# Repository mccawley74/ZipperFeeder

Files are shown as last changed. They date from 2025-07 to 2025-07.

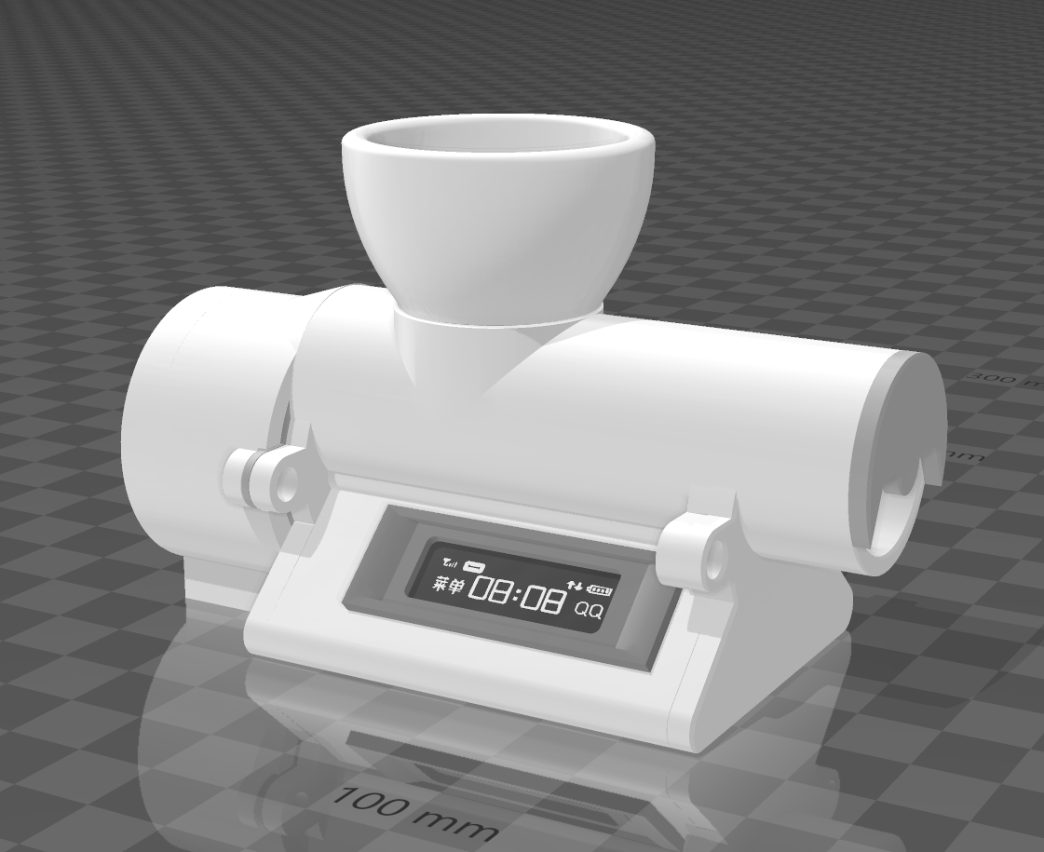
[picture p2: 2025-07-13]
Images/assembled.png

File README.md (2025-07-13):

Non-Commercial license You are free to: Share --- copy and redistribute
the material in any medium or format freely. Adapt --- remix, transform,
and build upon the material for any purpose, except commercially.

Attribution Heavily modified from: \"MiniFeeder\" By GK-3D
https://www.thingiverse.com/thing:4361894

# BACKGROUND
I made this feeder as I have a Pico Reef Tank (Two Gallon) with one
fish, my Gobi. Looking around for a small feeder was not successful,
most all were the size of my tanks lid blocked the light and held too
much food.

Since I had all these parts, I made the smallest feeder I could.

And if you are wondering why it is called Zipper Feeder, it is because I
have a Striped Goby that I named Zipper. You will see this name in the
OLED menu as well. I did make it so the name is a variable in code:
String fish_name = \"ZIPPER\"; Line 92 I believe, in
\"zipper_feeder.ino\"

## Pros
 1. Small, very small 2. Simi programmable feed schedule with OLED
screen 3. Nano feed rate. Good for 1-3 small fish 4. DIY abd fun to
build, unless you have sausage fingers :( 5. Customizable if you do any
3D modeling and/or Arduino development.

## Cons
1. Does NOT have an RTC clock. I.e. no time keeping, uses time since boot to track schedule.
2. Only programmable to feed every six hours, or every three hours. With option to skip nights.
3. The amount of food it dispenses is based on the Auger size. I included two:
    - auger_larger.stl Has larger spacing, allowing more food per rotation.
    - auger_smaller.stl Has smaller spacing, allowing less food per rotation.

You can print each individually or both with file \"auger_both.stl\" and
test each.

4. Hard to assemble due to small size. 5. Manual alignment of the Auger. Only needs done once. Could be added to code (Have a go!) 6. Some manual modifications needed. I.e OLED mounting, button location and hole, screw
choice.

7. No screw standard. I used what I had, what fit. The front cover is pass-through (Nut bolt) The rear cover and motor cover/motor mounting is
self threading screws.

8. NOT battery powered, needs USB 5v

NO: It does not overheat in such a small space. It really doesn\'t do anything until it feeds. The motor is external of the main chassis, runs only every 3 hours minimum, etc\... There is however a vented front cover \"front_cover_vented.stl\" if you are paranoid.

## BOM Item Description Cost

| Item |Description | Cost |
| --- | --- |  --- |
Control Board:  |  Arduino Pro Micro 5v                          |  $6.50 Ea.
Motor:          |  28BYJ-48 Stepper Motor                        |  $2.50
Motor CTRL:     |  ULN2003 Driver Board                          |  $2.50
Button:         |  Micro Momentary Tactile Push Button           |  $0.05
Wire:           |  30AWG 8-Color Tinned Copper Solid Cable       |  $0.10
Display:        |  0.91" I2C OLED Display SSD1306 128x32 3.3V/5V |  $4.00
Housing:        |  Overture PLA                                  |  $1.00

Per part prices are based off of Amazon and include the breakdown cost
used, I.e: - OLED screen comes as a two for \$8.00 - A spool of wire is
\$9.00 - The motor and motor control board come as a pair for \$5.00

If you search Amazon/AliExpress with the search term being the above
Description you should easily find the part(s)

Yes, you can buy a decent feeder for around \$20.00, but if you already
have some parts and you want a super tiny feeder, and love to make
stuff. Keep reading.

If you want the best automatic feeder I\'ve found to date, look at the
Petbank Store \"Automatic Fish Feeder\" It\'s is a round carousel style
USB re-chargeable feeder with LCD that lasts for weeks. Not affiliated,
just have two now for my larger tanks and they work great.

### ASSEMBLY: Sorta, Don\'t hate me after this part.
---
You will need thin wire to allow for the reduced space. I use 30AWG wire
in most all my Arduino projects. Specifically \"8-Color Electronic
Wire - 30 AWG Single Core, 250M Tinned Copper Solid Cable for Circuit
Boards & PCB\" You can find it on Amazon. Just search for the above
mentioned.

There is no schematic for this project. All connections are detailed in
the header comments of the Arduino code:
/Code/zipper_feeder/zipper_feeder.ino

The assembly takes the most time and patience. I did some tweaking of
the files after I assembled mine to make things a bit easier.

Things to note. There are two motor controller boards you will find on
Amazon/AliExpress, etc the first is a square type the other is a smaller
rectangle shape.


While the square type had better motor control when it came to the
smoothness of the movement at low speeds, the rectangle shaped board was
a lot easier to fit in the chassis. The Chassis was designed for the
square board so either will work. Your choice.

Both of these boards can be found with a motor on Amazon/AliExpress with
a motor. The motor will be: 28BYJ-48 Geared Stepper Motor DC 5V The
board will be one of: ULN2003 Driver Board, or L293D Motor Drive Module
DC4.5-25V

For either of the two motor control boards you choose, you will need to
cut down the connection header pins, or de-solder altogether. (I
de-soldered for best clearance)

### Assembly Steps:
1. Lay the printed chassis on your workplace.
2. Place the motor, Arduino, and OLED display on the left of the chassis.
3. Place the motor module to the right of the chassis.
4. Lay out your wire from the Arduino to the Motor Control board so as
there is enough to pass through the chassis and reach the control board.

5. Cut the motor wires down so that there is just enough length to also
reach the control board but still leave the motor with a good inch
clearance from the chassis. See image: motor-mounting.png You will want
enough slack, once the motor board in installed to pull the motor off
the auger. See Image: assembly-2.png for a cutaway chassis diagram.

6. Set the chassis aside and lay out the parts in the order shown in
image: wire-two.png Solder the motor wires to the control board, the
control board to the Arduino. The OLED to the Arduino (Leave wire slack)
etc\... The images should help.

7. Glue the main chassis to the Auger tube (CA Glue) Place the main
chassis on a flat surface and apply glue to the top of the chassis,
while holding the auger tube, place onto the top of the chassis and hold
in place until dry. The auger tube rear flange should butt up against
the rear main chassis. See: \"tube_alignment.png\"

You can temporarily mount the motor cover to the auger tube as the
bottom of the motor cover will lay flat against the work surface along
with the main chassis, this will allow the tube and chassis to remain
properly aligned with one another while the glue dries.

8. Mount the OLED, after the OLED in in place use CA Glue to align and
affix the screen bezel.

9. Align and mount your button. Use glue to hold in place. NOTE: You
will notice that the chassis STL does not have a button hole. The first
model I Made did not have any menu or programmability and thus no
button. I added it later and as such I simply drilled a hole and glued a
small Tactile switch I had in place. Feel free to use any button you may
have, put where you want (Fits) Or even use two buttons and update the
code. There are plenty of free GPIO ports to work with. I am sure the
code can be improved upon.

10. Insert the Arduino into the chassis. slide in and then to the rear,
making sure the USB port properly slides into the USB hole in the
chassis. Use a bit of PLA, toothpick, etc. to wedge the Arduino in
place. see image: board-mounting.png

11. Slide the motor control board into the chassis and install the
front cover.

12. Install the rear cover, making sure that the motor wires pass
through the slot in the cover.

13. Slide the Auger into the chassis tube and press into the motor,
aligning the slot in the auger to that of the motor. If too tight heat
the motor shaft so it more readily slides into the PLA Or ensure that
the Auger and motor shaft fit ahead of time.

14. Slide the motor_cover.stl over the motor and install screws to
secure the motor cover, and motor to the chassis. Again see images in
the images folder for help.

15. Use CA Glue to affix the hopper and Auger tube cap.

16. Connect to your computer and flash with the included code.

**NOTE:** The auger tube cap keeps the auger from accidentally coming off
the motor shaft and sliding out the end of the tube. While it does make
removing the Auger a bit more difficult as it can only exit the rear of
the housing after removing the motor cover, and motor, it does keep the
Auger in place.

If you use the smaller rectangle shaped motor control board it
will slide in from the same side of chassis as the Arduino (Left) At a
slight tilted angle.

As of now, there is no recess, or specific mount for the OLED. It will
just fit into the opening. from the inside of the chassis. Once you have
it in place, use CA Glue, hot glue, or a PLA pen to hold in place
permanently. (Or edit the STL files)

Be patient. I wasn\'t sure at first if all the parts would fit, and
fought for a while before coming up with the method shown in the images.
I did manage to fit the larger square control board before re-designing
the chassis and using a smaller board as de-soldering that many pins was
tedious and I figured anyone making one of these would hate me just a
little less.

If you leave the Arduino an inch outside the chassis (left), and the
motor control board 1 inch outside the chassis (right), and measure out
the wire length, and use half that length for the OLED, it will all
stuff in the chassis nicely.

It\'s all easy to put in but becomes a bit fiddly once the OLED is glued
in place as the Arduino board, and motor have only an inch or so of
play.

### MENU SYSTEM
---
1. Press the button once to enter the menu system.
2. Each press of the button will move to the next menu setting.
3. Hold the button down for one second to select that menu item

**NOTE:** If you reach the end of the menu it will round robin back to the
start.

Each menu setting is listed below as it appears on the screen.

#### Id Grouping Item
---
1. Menu \| Options Load Food
2. Menu \| Feed Feed Now
3. Menu \| Feed Every 6 Hours
4. Menu \| Feed Every 3 Hours
5. Menu \| Feed Feed at night
6. Menu \| Time Reset Timer
7. Menu \| Options Empty Feeder
8. Menu \| Options Exit Menu

For any given menu item above, hold the button down for one second to
select that menu item. There is no sub-menu and after selecting a menu
item the menu will exit.

A description of menu item selection is given below.

1. Load Food: This will aid in loading food into the feeder. Fill the
hopper and select this menu item. The auger in the feeder will rotate to
draw food to the end of the feeder, preparing for feeding.

2. Feed Now: Dispenses food

3. Every 6 Hours: When set the feeder will run a feed rotation every 6
hours or 4 times in a 24 hour period. See \"Feed at night\" to only feed
during day hours.

4. Every 3 Hours: When set the feeder will run a feed rotation every 3
hours or 8 times in a 24 hour period. See \"Feed at night\" to only feed
during day hours.

5. Feed at night: Skips the last 2, or last 4 feed rotations allowing
only daytime feeding. True = Food will dispense during nighttime feed
rotations. False = Food will only dispense during daytime feed
rotations.

6. Reset Timer: This is used to start the timer for feeding. Whatever
time it is when this is selected will be the start of the timer.

7. Empty Feeder: Runs the auger for 8 revolutions to help empty food
left in the feeder. You should first empty the hopper, then select this
option to assist with emptying the feeder of remaining food.

8. Exit Menu: Exits the menu and returns to the running display.

Example feeding schedule.
---
There is no clock in the Arduino Pro Micro, so
time is calculated in milliseconds since the board was booted, or since
the \"Reset Timer\" is selected.

Plug in the feeder at 9:00am, or select \"Reset Timer\" from menu at
9:00am to start the time rotation. You can start the feeder at any time
you want, 9:00 is used as an example.

Interval Feed at night | 6 Hour | False |
- Food rotations will be 9:00am , 3:00pm

Interval Feed at night | 3 Hour | False
- Food rotations will be: 9:00am , 12:00pm , 3:00pm , 6:00pm

Interval Feed at night | 3 Hour | True
- Food rotations will be: 9:00am , 12:00pm , 3:00pm , 6:00pm , 9:00pm ,
12:00am, 3:00am , 6:00am

**NOTE:** The feeder will not feed when first booted, or \"Reset Timer\" is
selected from menu. To initiate the first feeding, select \"Feed Now\"
from the menu. Subsequent feedings will occur at designated hour
intervals (6 hour or 3 hour)

Lastly: Do not print the files from /3MF Files/Assembled_Feeder.3mf The
individual .stl files are the most up to date. Use the
Assembled_Feeder.3mf for reference only whilst assembling the feeder.

Thank you, now go soak your poor fingers in some Palmolive soap and
relax.

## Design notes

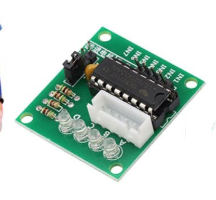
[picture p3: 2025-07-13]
Images/motor-control-boards_2.png

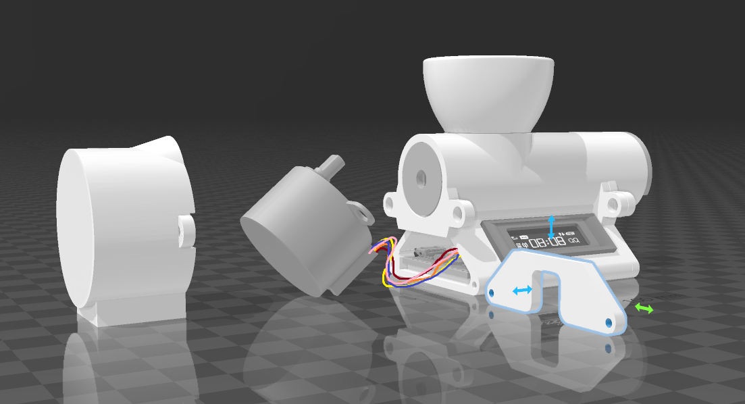
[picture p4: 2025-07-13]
Images/motor-mounting.png

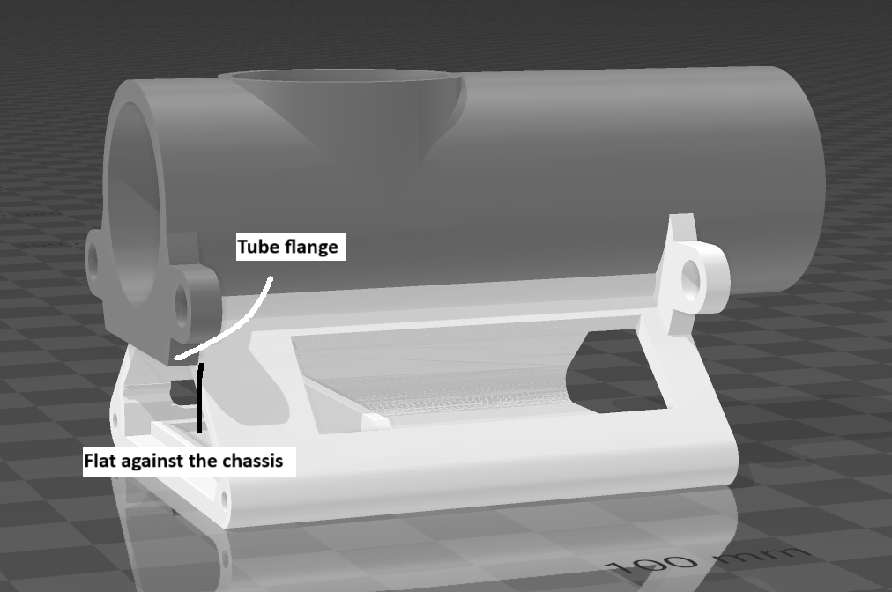
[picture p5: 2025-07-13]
Images/tube_alignment.png

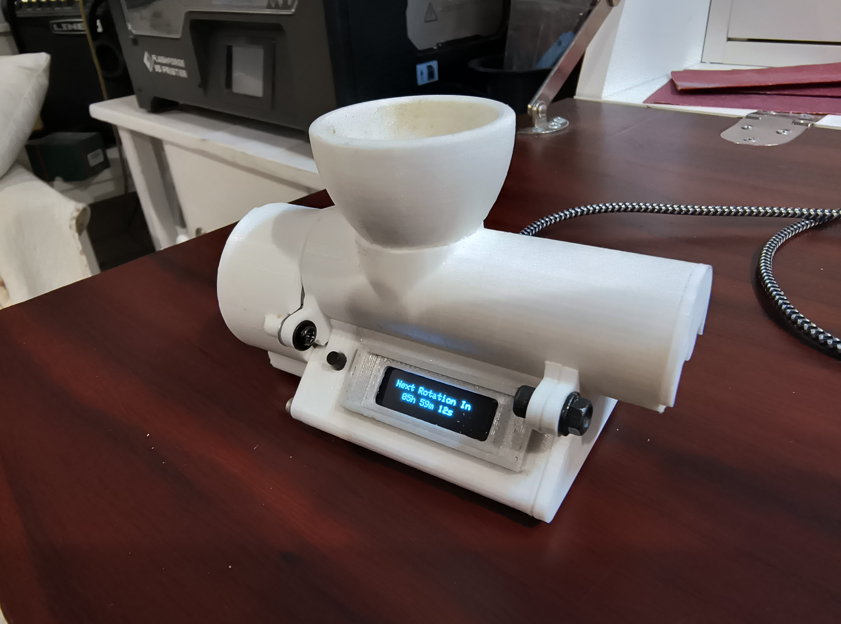
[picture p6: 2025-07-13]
Images/ZipperFeeder.jpg

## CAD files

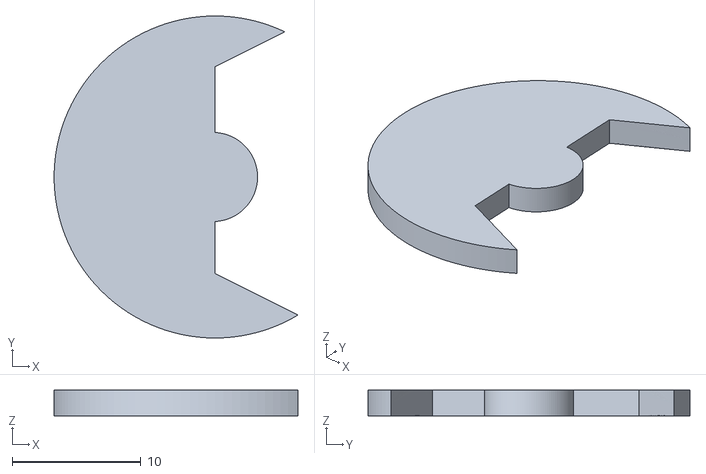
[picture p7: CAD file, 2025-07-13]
STL Files/auger_tube_cap.stl
18.9 x 25.0 x 2.00

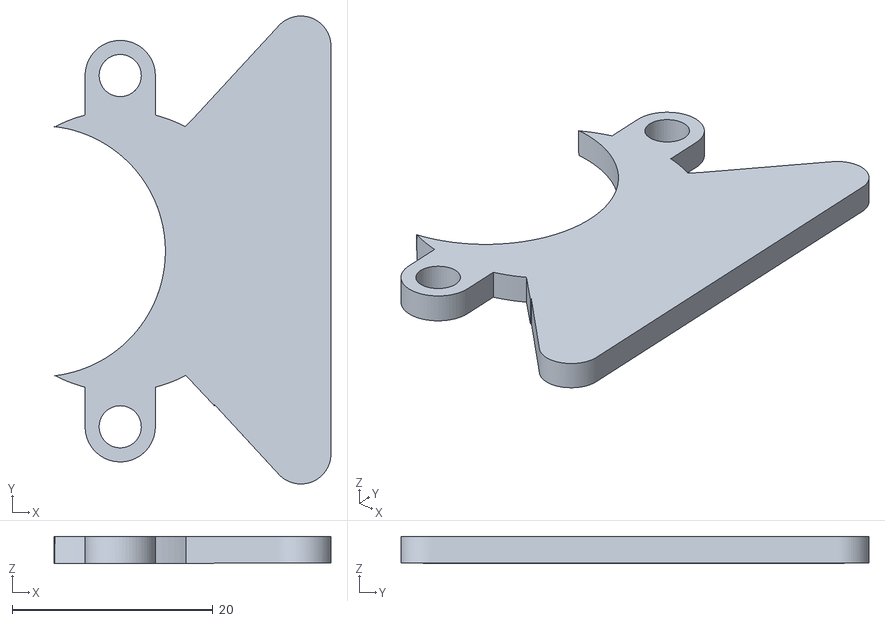
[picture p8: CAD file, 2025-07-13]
STL Files/front_cover.stl
27.6 x 46.6 x 2.70

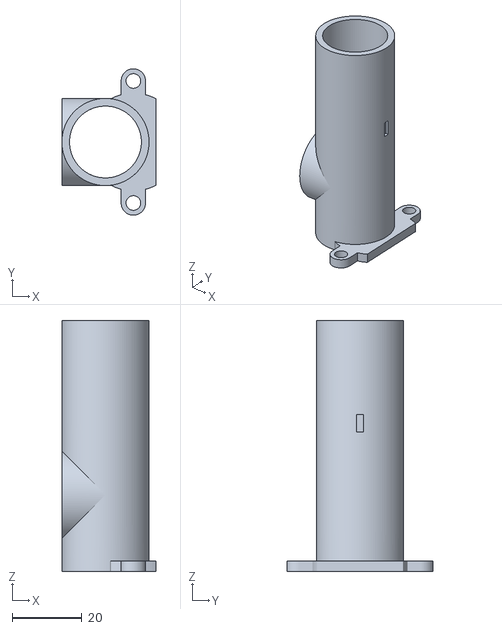
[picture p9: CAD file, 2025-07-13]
STL Files/auger_tube.stl
27.0 x 42.0 x 72.0

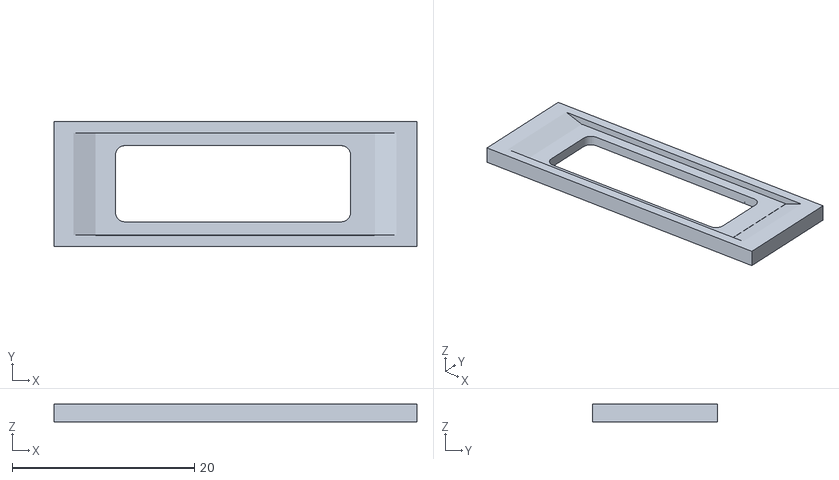
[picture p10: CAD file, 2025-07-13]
STL Files/display_cover.stl
39.9 x 13.7 x 1.98

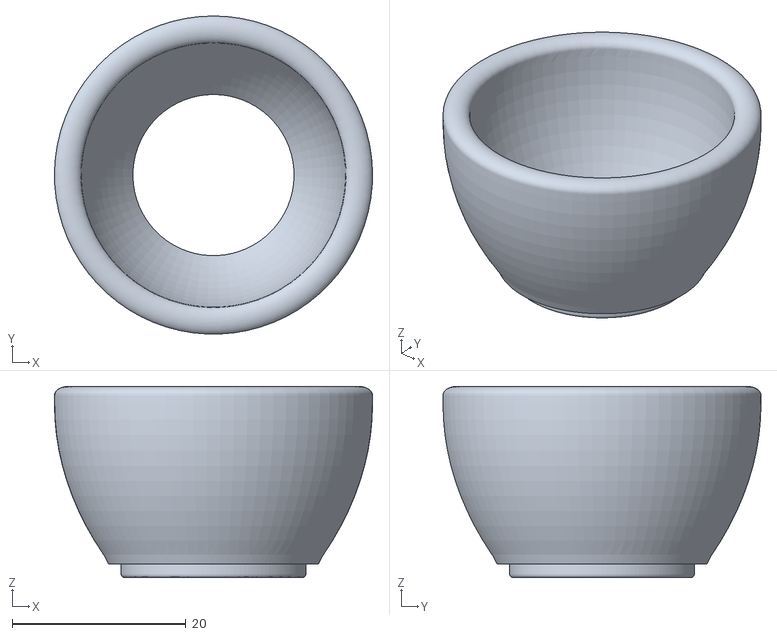
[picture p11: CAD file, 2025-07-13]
STL Files/food_hopper.stl
36.6 x 36.6 x 22.0

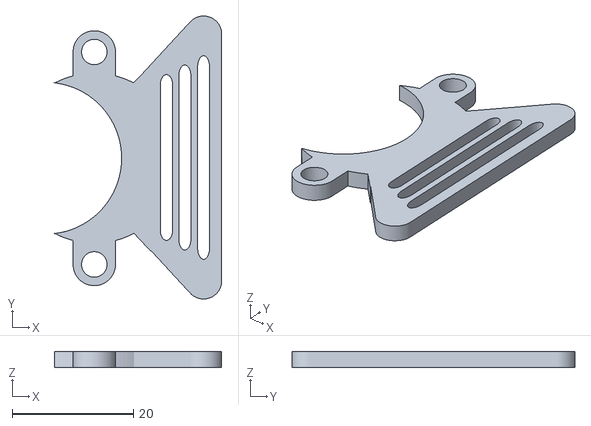
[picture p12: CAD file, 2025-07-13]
STL Files/front_cover_vented.stl
27.6 x 46.6 x 2.70
